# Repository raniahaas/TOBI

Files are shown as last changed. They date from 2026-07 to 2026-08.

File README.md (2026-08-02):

# TOBI
Telemetry, Orientation and Barometric Instrument Flight Computer used for the University of Cincinnati's Rocketry Club's Projects.\
TOBI_Logo

# Introduction
TOBI, from the Japanese word 飛び（とび「tobi」）meaning to soar, was born to serve as a custom avionics bay as a foundation for the University of Cincinnati's Rocketry Club's future space attempt, as well as a custom device personally. The overall goal for final development is to have a working custom flight computer that can log data, determine events, and fire pyrotechniques, all independently.

This repository is still in _**active development**_, but is intended as a clean starting ground to learn, teach, and develop further knowledge of avionics. 

| Goals | Method(s) of Execution |
| --- | --- |
| Multithreading | Using FreeRTOS, use the two cores on the ESP32-S3 to monitor and log events while another core stores data. This became a notable issue in past iterations where often data was missed, overlapped, or entirely logged improperly. |
| Event Logging | More specifically, events for apogee, main and drogue deployment, second-stage ignition, launch, and landing. |
| Pyrotechnics | Simulate the ignition of the second stage, wire cutters, and parachute deployment that current prefab electronics for model rocketry execute. This will become a full feature later on in the following year. |
| Wi-Fi Integration | Mostly, the ESP32 is known for its Wi-Fi capabilities. In our case, I will be utilising the Wi-Fi for data transfer and to check sensor continuity. This will be the main interface that the user uses to communicate with the device externally to the development. |
| Redundancy | Logging the sensors for data and comparing their redundancy with other computers or often COTS components to ensure our code is always performing to the best of its ability while also being the best option financially and methodologically.|

## Project Structure
```
tobiru/
├── data/
│   └── assets/          
│       └── TOBI_Logo.png
├── include/
│   └── flightState.h      # Hardware headers for the flight state
├── lib/                   # Project-specific libraries
├── src/
│   ├── startup/            
|       └── imu_init.cpp   # Initialise IMU datarates
|       └── imu_init.h
|       └── startupSeq.cpp # Start device and initialise accelerometer and barometer datarates; battery voltages
|       └── startupSeq.h
│   ├── globals.h          # Global elements
|   ├── globals.cpp
│   ├── main.cpp           # Task creations
│   └── wifiSetup.h        # Web dashboard with the Wi-Fi interface
├── test/                  # Unity test suites
│   ├── test_flightstate/
|       └── test_main.cpp
│   └── test_telemetry/
|       └── test_main.cpp
└── platformio.ini
```

## Device
| Insturment | Name |
| --- | ---- |
| Accelerometer | [Adafruit LSM6DSO32](https://www.digikey.com/en/products/detail/adafruit-industries-llc/4692/13250946) |
| Microcontroller | [XIAO SEEED ESP32-S3](https://www.digikey.com/en/products/detail/seeed-technology-co-ltd/113991114/19285530) |
| Barometer | [TE MS5611](https://www.digikey.com/en/products/detail/te-connectivity-measurement-specialties/MS561101BA03-50/5277445) |
| PCB | See KiCAD Files |
| Mosfet | [Toshiba T2N7002](https://www.digikey.com/en/products/detail/toshiba-semiconductor-and-storage/T2N7002BK-LM/5409245) |
| Additional elements | Battery terminal, 2-prong screw terminal, 4-prong screw terminal, resistors & transistors | 

## Project Status
- [X] Create multithreaded code for sensor logging (FreeRTOS)
- [X] Have a flight state machine for pre-launch, launch, and landing
- [X] Test functions before final implementation (Unity)
- [X] Local Wi-Fi server for live telemetry data and downloading post-flight data
- [X] PCB integration testing
- [ ] Use pyrotechniques for deploying main and drogue chutes
- [ ] Test flights!

## Building and Flashing Device
The native PlatformIO extension allows the user to flash to the device by simply validating the code and 'pushing' it onto the device. 
Flashing and validating code in Visual Studio Code with PlatformIO
You can additionally flash the code manually by:
```
# Build and upload firmware to the flight computer
pio run -e esp32s3 -t upload

# Open serial monitor
pio device monitor
```

## Flight State
There are three main flight states: startup, ready, and landing. Startup occurs as soon as the device is powered on and will switch to ready once all checks are complete. In the ready state, the user on the front-end server can arm and disarm the device to start recording instruments for flight. Once events are detected and landing has been determined, the device will enter landing mode and produce summary information as well as downloads for CSV files for the user. 

| State | Description |
| ----- | --- |
| startup |	Sensor initialization runs (runStartupSequence()), Wi-Fi starts up |
|ready |	Initialisation complete, device idle, user can access webpage |
| armed	| Event detection is live — launch/apogee/landing checks run every cycle in shutDown()|
| landed	| Landing confirmed; event detection stops, flight summary data is finalised|

Transitions are currently one-directional (no state is re-entered), driven by main.cpp on startup/arm and by the event detection logic on landing confirmation.

## Flight Events
Key flight events are detected by a pure, hardware-independent function (updateFlightState), so the same logic that flies on the device can also be validated on a laptop with no board attached.

| Event | Trigger Condition |
| ----- | --- |
|Launch |	Z-axis acceleration exceeds a threshold (~15 m/s²)|
|Motor Burnout | Gs drop and at least 0.5s have passed |
|Apogee |	Altitude drops more than 50m below the recorded peak|
|Landing | Altitude returns near launch altitude, acceleration stabilises near 1G, device is stable for 3+ seconds|

## Testing
Testing is natively done with the combination of PlatformIO and Unity, where instruments are stripped, and logic functions are tested. Flight-critical logic (launch detection, apogee confirmation, landing verification) is extracted into pure, hardware-independent functions.

```
pio test -e native -f test_flightstate
```
platformio.ini defines two environments inside of testing:
- esp32s3: the physical hardware board the main code runs off of
- native: emulates real hardware to test functions purely

## Safety
This project is intended for use in HPR (high-powered rocketry) and uses pyrotechniques to deploy parachutes and allow for second-stage ignitions. All safety protocols must follow NAR safety codes and are built in accordance with a recoverable HPR two-stage flight. Do not fire, wire, or test pyrotechnic channels without knowledge of the code, device, and user-controlled testing deployment.

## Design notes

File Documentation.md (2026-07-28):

# Beginnings: Multithreading and Sensors
Introductory code and LED development were done by following this article [here](https://randomnerdtutorials.com/esp32-freertos-arduino-tasks/).

Note that the ESP32 being used in the article is slightly different from the one I am using. I am currently running off of the ESP32-S3 by Seeed. 

This is the initial wiring I used following the article. The overarching idea is to specifically assign a core (1 in this case) to blink the LED every second.\ 
Working with one LED on a single core\
The largest trial and tribulation I noted here (other than simply learning how to work with a very basic hardware system) is that the GPIO number for the Seeed is different from the regular Arduino GPIO number. The indexing starts at 1, not 0, which did cause some hairs to be pulled. I then moved to actually working with two cores by using two separate LEDs, one blinking every second on core 1 and another blinking every half second on core 0.
Serial Monitor logging results of multithreading two LEDs.
Additionally, viewed similarly to the stack and heap, not exactly necessary currently, but for more advanced development further down the line, this will become handy.
Serial Monitor outputs of the stack and heap available

# PCB Practice and Development in KiCAD
This section initially follows the tutorials from [HTM Workshop](https://www.youtube.com/playlist?list=PLUOaI24LpvQPls1Ru_qECJrENwzD7XImd) on schematics, custom parts, and PCB design in KiCAD. Initially, this was not a critical piece for the development of TOBI, but overall, for my advancement of knowledge of integration with hardware and understanding the day-to-day activities of an embedded systems engineer, under my mentorship, this was deemed to be a critical step in my knowledge.
### Practising Schematics
The goal here was to re-create a schematic of an SPO2 module in KiCAD. This just helped me get a better lay of the land when it came to working with KiCAD, running the electrical rule checker, ensuring there are no connect flags properly placed, and the general wiring. 
Final SPO2 Module
Additionally, I also learned how to make custom symbols to be added into schematics. Definitely one of the more useful tidbits to know when working with some lesser-known avionics parts. 
Custom MAZ30102 Module for KiCAD
Learned a lot here that consistency is key; often when running checks, I'd run into issues with wiring when setting up the final PCB design. Ensuring everything is consistent saves a lot of hair. Truly covered a lot of bases here: final PCB design (without finishing touches, just drafting), vias, setting up PCB templates based on printing (from the templates [here](https://github.com/sethhillbrand/kicad_templates)), custom schematics for each part as well. 




Screenshot 2026-06-01 at 21 42 16 (2)

## Design and Final Schematics
[TOBI_schematics.pdf](https://github.com/user-attachments/files/28931927/TOBI_schematics.pdf)\
When it actually came to the final schematics for TOBI, it was a smooth process. The majority of the components I was easily able to use and find from previous projects' elements. However, I did run into issues with sourcing the ESP32 from Seeed and the Adafruit DSO32, which both ended up being schematics that I revised from similar components online. \
Edited Adafruit DSO32 Symbol from online sources.\
Another issue I was constantly running into as well with these custom symbols and footprints is that often when I retrieved the KiCAD files from GitHub, if I switched to another branch on the same repository (also known as this one), it would often cause issues with sourcing and retrieving those footprints. 
Custom Footprints in KiCAD, 'Library' displayed on left-hand side, but was often not displayed in the schematics or symbol editor.
One of the first things you should always consider when designing anything in engineering is your constraints, which I did not do this time. Right before reviewing my PCB design, I realised I never considered the fact of my board constraints and where I was placing threaded rod holes for the board. A best solution would be making a 36 mm minimum diameter board, but that is quite the constraint I did not realise would be an issue (in which I am saving for a later date). Out of my two current rockets I would be testing with, the smaller of the two has a 2" diameter for the e-bay.  
Quick PCB layout with the 2in diameter board.
Open rocket design for the smaller kit rocket.
This does pose some great questions on further development, which leaves me with a lot of research and inquiry to do. The first option I can think of is just to make the board double-sided (hence why there are two circles in the image, just for a general feel). Considering how the project has done this previously, I did not consider the fact that the pins from the ESP and the DSO32 would go through the board, meaning this may cause more of an issue stacking the two than I originally thought. I think it is possible to a degree, if I truly do move everything around, but then I'd run into issues with routing, even with vias and such; there would be elements on the bottom that need to be routed up through to the ESP, which may just be exceeding the knowledge I currently have. Another option I considered was giving up and making one solid board to place horizontally instead of vertically inside of the e-bay. The largest issue here now becomes the coding and measurements. It is a lot easier to work off of 0º than +- 90º. When it comes to collecting telemetry data, lock-out angles, & recording information, it becomes an issue. 

### UI Design
Moving on from multithreading, my next focus was then on the front-end since this not only clears up direction for what I need to be monitoring and recording, but also while waiting on the final PCB to be done to test all sensor functions. The majority of my inspiration came from previous use with the Featherweight Altimeter Blueraven App as well as another app called Euristiq. A fun easter egg regarding the colouring is the use of Gunship Grey (676C73), which is the paint colour used on the B-2 Spirit, which is the plane that got be re-introduced into aviation and rocketry. Overall color pallet consists of 6 colors: #C83408, #F5ECD3, #FB961B, #191553, #1E2719, and #676C73. 
Full Figma UI design
I won't go too in-depth into the specifics of the overall UI design; however, I will go through the three main states and their designs. The three states are: Start-up, Ready/Armed, and Landed. First, let's look at our startup. I'm using colours here to help be an indicator of status when it comes to blocks as well as text colours. There is a sort of stoplight system I am using with the Orange, Green, and a lighter shade of the 191553 for a Go, Yield, and Stop system. This is displayed in both the text as well as in the various colored circles littered across each page. Overall system status is displayed in the upper right-hand corner. The full Figma sketch can be viewed [here](https://www.figma.com/board/tCNcCzarbBjb5qSviv4QY5/Untitled--Copy-?node-id=0-1&t=Rhq6jWPLQq2U6YhN-1).
Start up UI design in Figma.\
Similarly, with our Armed and Ready states, we are using colour to display the current status. This status should automatically populate once the start-up sequence is officially complete. The only difference between our Armed and Ready states is the colors--helping to distinguish with the computer determine if it should start looking and watching for a flight to begin. 
Ready and Armed status in Figma.\
Finally, the landing page is where the bulk of the important information is. Often, since we are retrieving this through a WiFi signal and since you stand far from the pad (and through a carbon fiber/fiber glass body tube), it is only when checking the device and arming it that you will see any data. This final screen is the most important since it includes the overall download for the CSV files that will be written from the computer, but also overall quick stats so you can see the key figures from the CSV file. Personally, my favourite as well is an overall curve from launch to landing, which will be a unique challenge to code on the backend.
Landed status in Figma.

# Intermediary: Soldering & Boards
For testing, I ended up soldering pins onto the Adafruit DSO32; this was not only great practice for later when it comes to the actual PCB board, but in general. I had messed up the pins a couple of times since I was originally using unleaded solder instead of leaded and not being overly proficient with soldering caused some issues. Some were not entirely connected, did not contain enough solder, or I had accidentally soldered multiple pins together. Luckily, it was a pretty easy fix and swap to do this properly.\
Unleaded solder of the DSO32\
I had a small setup at my desk that I used to solder, using a space heater with a fan option, my actual soldering iron, and a breadboard to help hold the device in place. Not pictured is my phone as well, on a phone stand, which I used the flashlight for to help focus the light better and give me a cleaner view with the microscope. The flashlight helped tremendously once I had started using it and made the process go by a lot quicker with higher accuracy.\ 

### Final PCB Design
For the most part, the final design went smoothly- the biggest issues arrived after the DRC and when finally sending the Gerber files to JLC PCB. Mainly, the DRC had a lot of issues regarding clearance violations, items shorting, thermal relief connection to zone incomplete, front/back solder mask aperture bridges items with different nets. Clearance and shorting were both easy fixes; they required some more moving around parts and changing the overall nets. However, the thermal relief and solder mask aperture were a little more difficult to understand and fix. They did end up being simple fixes like editing the number of thermal relief holes and adding extra vias to help connect ground points. Additionally, when uploading to JLC, I learned you have to use mounting holes rather than edge cuts, as when uploading the Gerber file, it then sees that as parts rather than a board with cuts.
Front Wiring Design.
Back wiring design.
Front 3D model
Back 3D model
JCL PCB 3D model

## WiFi Integration and testing with breadboard
All of my initial coding was done on [CodePen](https://codepen.io/) to give me faster, live editing of pure HTML without worrying about setting up an environment to run and test this code in. Except for the landing chart, pretty much all is true to the original design that I created in Figma. One notable difference, at least for me, was the fact that I was not able to accurately create the darker grey surrounding boxes for each of the devices being monitored, which is just a result of how I had set up the nesting between each of the elements (has to do with the absolute and relative positioning but then throws off the dynamic part of this). For another iteration of this flight computer's front end, I would love to see if I am able to integrate Svelte at all, since that is mainly where all my front-end development has been in with my courses at the University of Cincinnati. I am using the LittleFS system to mount and write to the CSV (which I will still be doing later in another branch, not the wifi development), and so far have had minimal issues with actually setting that up due to my previous work on a similar setup. 
Serial Monitor displayed information regarding startup and the WiFi server.
Local WiFi Hosting for TOBI, including password protection.
Main startup landing screen, including live data.\
In regard to the live updating, it seems to be working smoothly. You can test the accelerometer by simply moving the board and watching it refresh every second with updated information. Without having the final PCB done, I cannot confirm the battery voltage and/or the barometer data since neither is hooked up currently to the breadboard, but the accelerometer is working smoothly.

# Final Developments
## CAD and E-Bay
All CAD development here is in Fusion360; the goal was to create a rough sketch to have an idea of what the final e-bay should look like and then, from there, create parts individually to print on my A1-Mini.\
Overall e-bay 3D model
Keeping the e-bay vertical was the largest issue that I was concerned with; previously, I had used two 9V batteries housed on a vertical component and on the other side had attached two stratologgers (although that flight had failed, it still worked accordingly with parachute deployment). However, TOBI itself, as a board, sits around the threaded rods and hence needs a housing unit within the electronics bay to attach the LiPo batteries to and hold in place. After some research online, I created this version where there are separate 'boards' creating separation between parts. The LiPo batteries have a compartment they are placed into before placing the top components. There are two options here as well for attaching the batteries to the board: either hard, creating a hole inside of the separation disk in between, or later drilling through the PLA. The PCB will then sit on top of that, keeping it close to the top in case of emergency where the user needs quick access to removal and insertion. The bottom section for now is being left empty, but is a great place for an additional payload and experiment. Spacers are then designed to go around the threaded rods to help house and keep the whole unit in place. Two couplers are on the top and bottom to hold the entire device in place and lock in the threaded rods with the e-bay.  
Closer look at the PCB placement in the e-bay
It ended up taking a couple of modifications to get the couplers correct, with them mainly being undersized based on forgetting the assumption that this does not need a second layer of reinforcement like previous electronics bays I have designed. Since this is pure carbon fibre, it is strong enough to withstand any external acting forces without re-enforcing. After the third version of the coupler, I additionally added threaded rod holes (for a fourth version), LiPo and a separating disk for the inner tube, and more specific measurements for the covers of the internal threaded rods.\
The several 3D printed iterations of couplers.
Final coupler iteration before the threaded rods inside on the electronics bay
Final Iteration for the coupler with the inserted threaded rod holes.
I went through two iterations with the LiPo holders; I noticed that the housing unit was too close to the threaded rod holes and was additionally a little thin on the walls. I slightly adjusted these to be slightly thicker and flipped the unit to sit opposite the threads.
Iterations of LiPo housing unit for electronics bay.
### PCB arrival and Soldering
PCBs came in looking amazing! I had chosen for the overall colour to be red to keep with the theme as a nod to UC and the whole project stemming from UCRC. Although I had already practised soldering earlier with pins on the DSO32, this would be slightly different as I would be using surface mounts (resistors, transistors, and surface-mounted elements like the barometer), which would require hot air soldering instead of regular iron soldering. With new tasks came new materials required to be purchased, so actually soldering the device was delayed by another week more so than I had hoped. 
Back of the final PCB design from JLC PCB
Front of the final PCB design from JLC PCB
One issue I began to notice as I went to place the regular iron devices on the PCB (which later I realised I should not have done first, as the battery terminal and screw switches are likely to melt under the hot air) was that the sizing for the DSO32 was slightly off, making the pin holes millimetres too far to fit snugly. This caused a new cause for concern; this error, I believe, was most likely due to the fact that there is no sizing information listed on Adafruit's website or in the datasheet for the LSMDSO32. Although within the datasheet for the DSO32 are also the LSM6DSOX and ISM330DHCX, which list the sizes for the overall board and the pinouts. Even if I had followed this graph, the pinouts would have been correct, but I measured from edge to edge rather than from pinout to pinout or pinout to edge, leaving a slight give on each side concerning the rest of the board.
Adafruit's Datasheet for the LSMDSO32, LSM6DSOX, and ISM330DHCX
Initially soldered elements on the PCB.
DSO32's width being too small for the large pad size.

### Unit Testing
Although this project has helped me gain knowledge in avionics, embedded systems, PCBs, and an overall understanding of electronics, an additional goal was to further pursue preparation for industry. After researching several positions and keeping track of languages, expected responsibilities, and additional requirements, one recurring responsibility that I realised I had a gap of knowledge in was unit testing. I have previously done unit testing in my co-ops and in other capacities with personal projects; my co-op had used proprietary software, and my own projects were more case tests written natively in the language I was working in. After some research, I came down to two options: Docker and [Unity](https://github.com/ThrowTheSwitch/Unity) (not the engine). After getting sufficiently through using Docker, I realised that Unity was actually native to Platformio and would create easier integration when it came to case testing, and I later switched. However, the biggest issue I will always run into with unit testing is edge cases; these are the most critical since these devices often deal with pyrotechniques, ensuring there isn't a false launch could be detrimental to a flight and cause early parachute deployment (all launches in HPR are manually controlled by a RSO for L1 and L2 launches, more experimental can occur through Tripoli and L3 but for our purposes there can be no false ignition of a motor only early deployment of parachutes and e-matches). To help combat this, I write truth tables in addition to the Unity tests to help demonstrate clearly, based on given information, how the device should perform, then confirm with the Unity code that the device is performing as stated. 
Unit testing truth tables for each function written in Unity.
Final testing for initial unit testing in Unity natively in Platformio.

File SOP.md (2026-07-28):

# Standard Operating Procedure of TOBI
This is a comprehensive checklist for TOBI, a custom avionics flight computer used for HPR (high power rocketry) model rockets. This device is for logging and saving instrument data only, not pyrotechnic parachute deployment. 
## Pre-launch Items:
- Custom Avionics bay
- PCB (ESP, DSO32, barometer)
- LiPo batteries
- USBC cable
- Laptop
- Electronics screwdriver
- Electrical tape

Items to test before launch day:
- Device activates
  - TOBI correctly allows arming device
  - Powers on WiFI & users can connect
  - Live data is running
  - Data rate values are correct
  - TOBI fully runs startup without errors
    - TOBI ensures battery voltage ensure LiPos are charged
- Assembly
  - Ensure no parts on PCB are loose
  - Tighten screw terminals
  - WiFi can be accessed through body tube
- Ensure packing for transit will not cause any items on device to come loose

## Launch Day Procedure:
- Check battery voltages
- Ensure TOBI powers on
  - Ensure live data is running properly
- Lock and load device into ebay
  - Ensure screws are tightened
  - 
### Pad Operations 
**DO NOT ARM DEVICE UNTIL ON PAD**
- Check WiFi Operations
- Once the rocket is on the rails and ready to launch after hooking up the motors, then arm the device for flight

## Recovery
- Ensure all data is downloaded to the user's device before shutting down electronics
- Double-check both CSV files have been downloaded

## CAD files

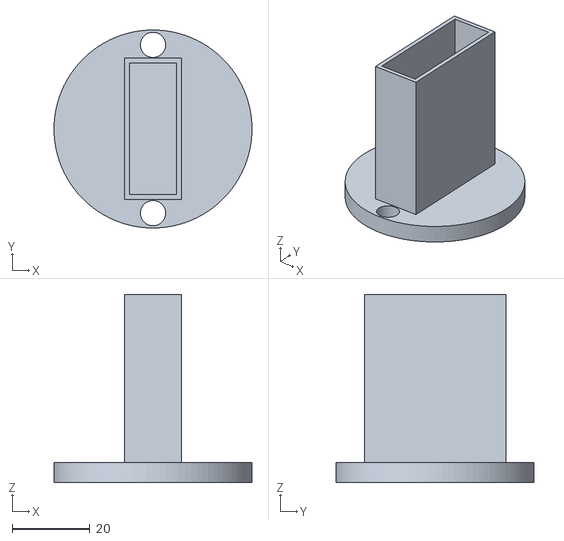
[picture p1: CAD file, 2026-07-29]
CAD_files/testing/LiPo_Holder_TOBI.stl
50.8 x 50.8 x 48.3

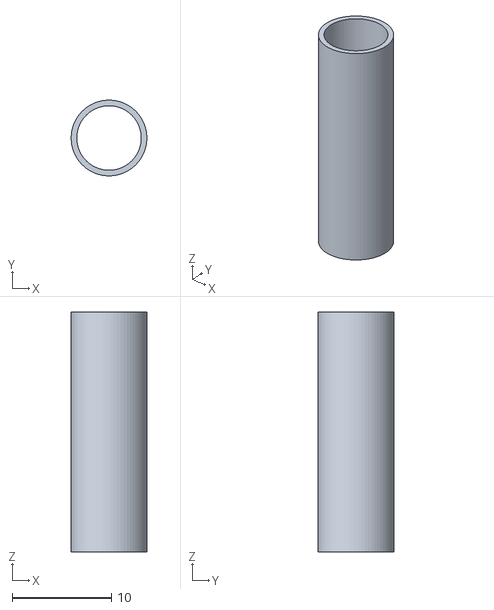
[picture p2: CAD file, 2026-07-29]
CAD_files/Threaded_Rod_Cover.stl
7.62 x 7.62 x 24.1

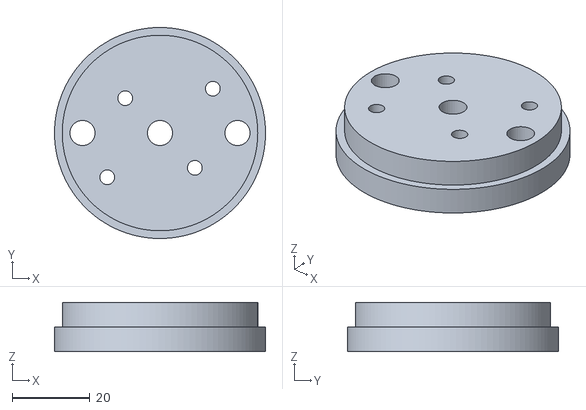
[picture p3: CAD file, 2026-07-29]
CAD_files/TOBI_cupler.stl
54.4 x 54.4 x 12.7

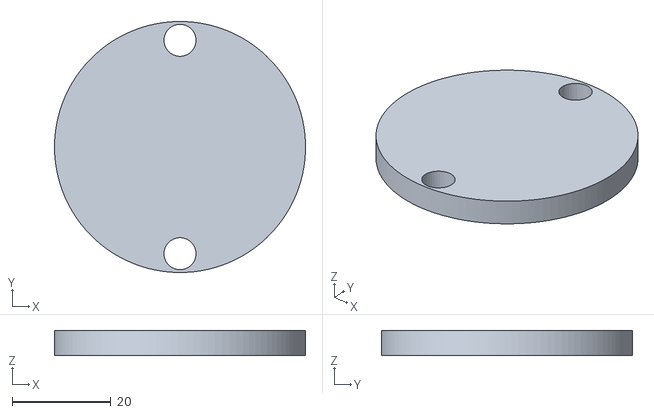
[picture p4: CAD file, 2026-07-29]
CAD_files/Flat_TOBI.stl
50.8 x 50.8 x 5.08

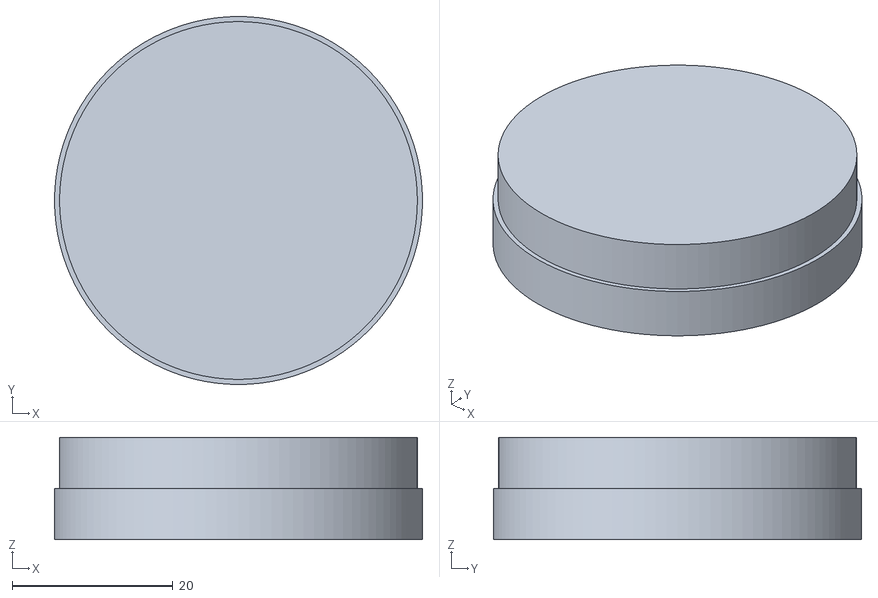
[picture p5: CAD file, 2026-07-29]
CAD_files/testing/TOBI_cupler.stl
45.7 x 45.7 x 12.7

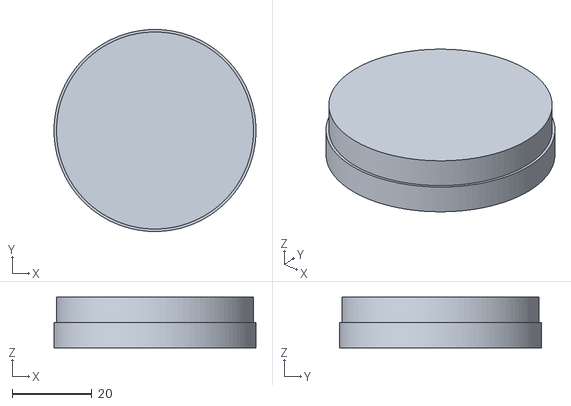
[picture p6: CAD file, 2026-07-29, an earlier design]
CAD_files/testing/TOBI_cupler (1).stl
50.8 x 50.8 x 12.7

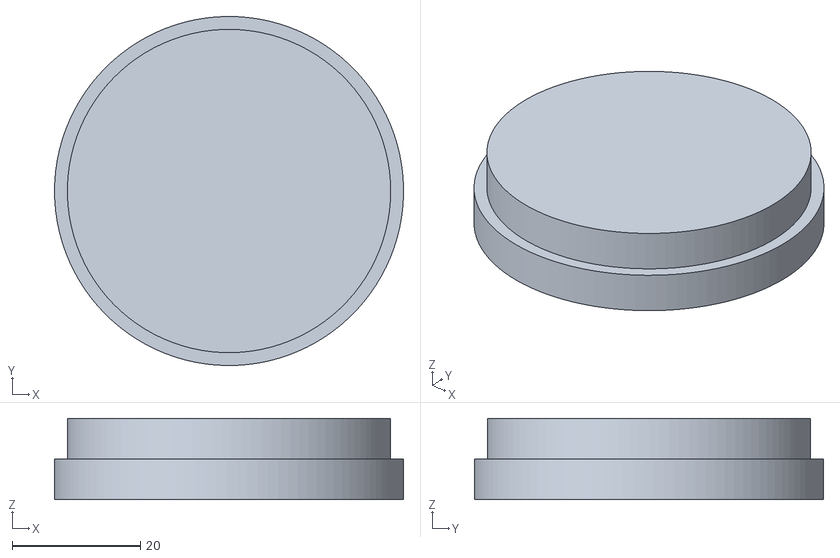
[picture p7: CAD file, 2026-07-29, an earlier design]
CAD_files/testing/TOBI_cupler (2).stl
54.4 x 54.4 x 12.7

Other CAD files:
CAD_files/LiPo_Holder_TOBI.stl

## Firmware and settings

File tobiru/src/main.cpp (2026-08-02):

/**
05/22/2026 - RH - Basework for multithreading integration
06/02/2026 - RH - Fixes to the RTOS declarations
06/14/2026 - RH - Added Startup sequence for IMU
06/14/2026 - RH - Battery Voltage display for serial log
06/16/2026 - RH - Testing for IMU; without battery testing independently
                - Moved Startup function to separate file
06/30/2026 - RH - Wired flightStatus transitions for WiFi dashboard
07/06/2026 - RH - Edits for incoorperating global variables
*/

#include <Arduino.h>
#include <Adafruit_LSM6DSO32.h>
#include <MS5611.h>
#include "startup/startupSeq.h"
#include <SimpleBatteryMonitor.h>
#include "globals.h"
#include "wifiSetup.h"
#include "fileLogging.h"


//Tasks
TaskHandle_t TaskFileLogging;
TaskHandle_t TaskEventLogging;
TaskHandle_t TaskUserTests;
TaskHandle_t TaskShutdown;
TaskHandle_t TaskIMU;
TaskHandle_t TaskBaro;
TaskHandle_t TaskBattery;

const int led1 = 3;
const int led2 = 5;

//Pyro pins for main and drouge; dont forget about offset when testing
const int PYRO_DROUGE = 5;
const int PYRO_MAIN = 9;

//Landed state variables
static float         maxAltitudeSeen    = 0;
static float         launchAltitude     = 0;
static bool          launched           = false;
static bool          apogeeReached      = false;
static unsigned long landedConfirmStart = 0;
static bool burnoutLogged = false;
static bool drogueDeployed = false;
static bool mainDeployed = false;
static unsigned long landingConfirmed = 0;
static unsigned long burnoutTime = 0;

//IMU writing
void imuWrite(void *pvParameters) {
  for (;;) {
    sensors_event_t accel, gyro, temp;
    dso32.getEvent(&accel, &gyro, &temp);

    //Write into globals to modify and grab
    g_accelX = accel.acceleration.x;
    g_accelY = accel.acceleration.y;
    g_accelZ = accel.acceleration.z;

    g_gyroX  = gyro.gyro.x;
    g_gyroY  = gyro.gyro.y;
    g_gyroZ  = gyro.gyro.z;

    logSensors();

    vTaskDelay(pdMS_TO_TICKS(100)); //10Hz
  }
}

//Barometer
void readBarometer(void *pvParameters) {
  for (;;) {
    //Once surface mounts are applied test
    // g_barometer = baro.getPressure();
    vTaskDelay(pdMS_TO_TICKS(100));
  }
}

//Event logging
void writeEvents(void *pvParameters) {
  for (;;) {
    if (flightStatus == "armed") {

    }
  }
}

//File logging
void fileLogging(void *pvParameters) {
  for (;;) {
    // log into csv file
    //csvReady = true; for download
    vTaskDelay(pdMS_TO_TICKS(100));
  }
}

//Landing detection and shutdown
//Landing detection will be separate but required for shutdown as well
void shutDown(void *pvParameters) {
  for (;;) {

    if (flightStatus == "armed") {

      float az  = g_accelZ;
      float alt = g_barometer; //replace with real altitude from baro


      //Detect launch when Z accel spike <1.5G
      if (!launched && az > 15.0f) {
        launched       = true;
        launchAltitude = alt;
        logLaunch();
        Serial.println("LAUNCH DETECTED");
      }

      if (!launched) {
        vTaskDelay(pdMS_TO_TICKS(50));
        continue;
      }

      //Calculate motor burnout based on Gs dropping and at least 0.5s passing
      if (!burnoutLogged && loggingTime() > 500) {
        if(az < 12.0f) {
            burnoutTime = loggingTime();
            burnoutLogged = true;
            logEvents("MOTOR BURNOUT", "Accelerometer", "Acceleration dropping post launch, motor burnout occuring.");
            Serial.println("Motor burnout detected!");
        }
      }

      //Track altitude for apogee
      if (alt > maxAltitudeSeen) {
        maxAltitudeSeen = alt;
      }

      //Detect apogee when device droppes 50m below the peak altitude
      if (launched && !apogeeReached && (maxAltitudeSeen - alt) > 50.0f) {
        apogeeReached = true;
        g_apogee = maxAltitudeSeen;
        logEvents("APOGEE", "Barometer and Accelerometer", "Altitude dropping at least 50 meters below max recorded height.");
        Serial.print("APOGEE DETECTED: ");
        Serial.println(g_apogee);
      }

      //Detect landing when near ground state and stable for 3+s 
      if (apogeeReached && !drogueDeployed) {
        digitalWrite(PYRO_DROUGE, HIGH);
        delay(500);
        digitalWrite(PYRO_DROUGE, LOW);
        drogueDeployed = true;
        g_drogue = alt;
        logEvents("DROGUE_DEPLOYED", "Pyro & Barometer & Accelerometer", "Drogue deployment after e-match.");
        Serial.println("Drogue Deployed!");
      }   

      //Main deployment
      const float MAIN_DEPLOY_ALT = launchAltitude + 150.0f;
      if(drogueDeployed && ! mainDeployed && alt < MAIN_DEPLOY_ALT) {
        digitalWrite(PYRO_MAIN, HIGH);
        delay(500);
        digitalWrite(PYRO_MAIN, LOW);
        mainDeployed = true;
        g_main = alt;
        logEvents("MAIN_DEPLOY", "Pyro & barometer", "Main pyros have been fired");
        Serial.println("MAIN DEPLOYED");
      }
    
      //Landing detection
      if(mainDeployed) {
        bool nearGround = (alt < launchAltitude + 20.0f);
        bool stable     = (abs(az - 9.81f) < 1.0f);

        if (nearGround && stable) {
          if (landedConfirmStart == 0) {
            landedConfirmStart = millis();
          } else if (millis() - landedConfirmStart > 3000) {

            g_timeToApogee = apogeeReached ? (float)loggingTime() : 0;
            g_timeToMain = mainDeployed ? (float)loggingTime() : 0;

            flightStatus = "landed";
            Serial.println("LANDED");
          }
        } else {
          landedConfirmStart = 0;
        }
      }
    }

    //20 Hz for eventes
    vTaskDelay(pdMS_TO_TICKS(50)); 
  }
}


void userTests(void *pvParameters) {
  for (;;) {
    vTaskDelay(pdMS_TO_TICKS(1000));
  }
}

void setup() {
  Serial.begin(115200);
  delay(3000);

  Wire.begin(5, 6);

  //PYRO pins
  pinMode(PYRO_DROUGE, OUTPUT); digitalWrite(PYRO_DROUGE, LOW);
  pinMode(PYRO_MAIN, OUTPUT); digitalWrite(PYRO_MAIN, LOW);

  //Intialise state
  flightStatus = "startup";

  runStartupSequence();
  startWifi();
  loggerInit();

  flightStatus = "ready";

/*
  Core 0:
    Used for all event logging
      File logging
      Events
      User tests
  Core 1:
    All fetching from instruments
      IMU
      Accel/Baro
  */

  //Core 0 Tasks                 
  xTaskCreatePinnedToCore(writeEvents,   "eventLogging", 8192, NULL, 2, &TaskEventLogging, 0);
  xTaskCreatePinnedToCore(fileLogging,   "fileLogging",  4096, NULL, 1, &TaskFileLogging,  0);
  xTaskCreatePinnedToCore(userTests,     "TestMode",     4096, NULL, 1, &TaskUserTests,    0);
  xTaskCreatePinnedToCore(shutDown,      "PoweringOff",  4096, NULL, 1, &TaskShutdown,     0);
 
  //Core 1 Tasks
  xTaskCreatePinnedToCore(imuWrite,      "imu",          4096, NULL, 2, &TaskIMU,          1);
  xTaskCreatePinnedToCore(readBarometer, "barometer",    4096, NULL, 1, &TaskBaro,         1);   

}

void loop() {
  WiFiInterface(); 
}

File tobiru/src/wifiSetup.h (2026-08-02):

/**
06/16/2026 - RH - Moved code to be independent in main
06/30/2026 - RH - Started integration of CodePen HTML setup
06/30/2026 - RH - Fixed JSON shape, string quoting, CSS dedup, function scope
07/06/2026 - RH - Edits for incoorperating global variables as well as more HTML edits
*/
#pragma once
#include <WiFi.h>
#include <WiFiAP.h>
#include <LittleFS.h>
#include "FS.h"
#include "globals.h"
#include "fileLogging.h"

#include <SimpleBatteryMonitor.h>
#include <Adafruit_LSM6DSO32.h>

const char *ssid     = "TOBI";
const char *password = "password";

WiFiServer server(80);

//Full HTML code
const char homePage[] PROGMEM = R"=====(
<!DOCTYPE html>
<html lang="en">
<head>
<meta charset="UTF-8">
<meta name="viewport" content="width=device-width, initial-scale=1.0, viewport-fit=cover">
<link href="https://fonts.googleapis.com/css2?family=Ubuntu+Sans+Mono:ital,wght@0,400..700;1,400..700&display=swap" rel="stylesheet">
<title>TOBI</title>
<style>
  * { margin:0; padding:0; box-sizing:border-box; }

  html, body {
    background:#191553;
    font-family: -apple-system, BlinkMacSystemFont, 'Segoe UI', sans-serif;
    height:100%;
    overflow:hidden;
  }

  #app {
    display:flex;
    flex-direction:column;
    height:100vh;
    height:100dvh;
  }

  .topbar {
    display:flex;
    align-items:center;
    justify-content:space-between;
    padding:12px 16px;
    padding-top:max(12px, env(safe-area-inset-top));
    background:#191553;
    border-bottom:1px solid rgba(255,255,255,0.06);
    flex-shrink:0;
    z-index:10;
  }

  .logo {
    height:28px;
    display:flex;
    align-items:center;
  }

  .logo img {
    height:100%;
    width:auto;
    display:block;
  }

  /* Fallback text if logo hasn't loaded yet */
  .logo-fallback {
    color:#F5ECD3;
    font-size:14px;
    font-weight:700;
    letter-spacing:2px;
  }

  .topbar-right {
    display:flex;
    align-items:center;
    gap:8px;
  }

  .time {
    font-size:11px;
    color:#F5ECD3;
    letter-spacing:0.5px;
    font-variant-numeric: tabular-nums;
  }

  .status-light {
    width:14px;
    height:14px;
    border-radius:50%;
    flex-shrink:0;
  }

  .light-off  { background:#C83408; }
  .light-on   { background:#7FCB8F; }
  .light-busy { background:#FB961B; }

  .pulse-dot { animation: pulse 1.6s ease-in-out infinite; }
  @keyframes pulse { 0%,100%{opacity:1} 50%{opacity:0.4} }

  .scroll-area {
    flex:1;
    overflow-y:auto;
    -webkit-overflow-scrolling:touch;
    scrollbar-width:none;
    padding:14px 14px;
    padding-bottom:max(24px, env(safe-area-inset-bottom));
  }
  .scroll-area::-webkit-scrollbar { display:none; }

  .card {
    background:#676C73;
    border-radius:5px;
    padding:14px 16px;
    margin-bottom:12px;
  }

  .card-label {
    font-size:11px;
    color:#D0F3D3;
    letter-spacing:0.5px;
    margin-bottom:8px;
    text-transform:uppercase;
  }

  .banner {
    background:#F5ECD3;
    border-radius:14px;
    padding:14px 16px;
    margin-bottom:12px;
    display:flex;
    align-items:center;
    justify-content:space-between;
  }

  .banner-text {
    color:#191553;
    font-size:14px;
    font-weight:600;
    line-height:1.3;
  }

  .toggle-btn {
    width:48px;
    height:48px;
    border-radius:50%;
    border:none;
    display:flex;
    align-items:center;
    justify-content:center;
    font-size:10px;
    font-weight:700;
    letter-spacing:0.5px;
    color:#F5ECD3;
    cursor:pointer;
    flex-shrink:0;
  }

  .toggle-off { background:#C83408; }
  .toggle-on  { background:#7FCB8F; color:#191553; }

  .sensor-value {
    font-size:20px;
    font-weight:700;
    color:#312F29;
    text-align:center;
    font-variant-numeric: tabular-nums;
    background:#D0F3D3;
    border-radius:5px;
    border:2px solid #88C493;
    padding:6px 0;
  }

  .triple-row {
    display:grid;
    grid-template-columns: 1fr 1fr 1fr;
    gap:8px;
  }

  .triple-item {
    background:rgba(245,236,211,0.08);
    border-radius:10px;
    padding:10px 6px;
    text-align:center;
  }

  .triple-axis {
    font-size:10px;
    color:#FFFFFF;
    margin-bottom:6px;
    text-transform:uppercase;
    letter-spacing:0.5px;
  }

  .triple-val {
    font-size:15px;
    font-weight:700;
    color:#F5ECD3;
  }

  .triple-unit {
    font-size:9px;
    color:#F5ECD3;
    opacity:0.5;
    margin-top:2px;
  }

  .dl-row {
    display:flex;
    align-items:center;
    gap:10px;
  }

  .dl-btn {
    flex:1;
    background:#F5ECD3;
    color:#191553;
    border:none;
    border-radius:10px;
    padding:12px 0;
    font-size:13px;
    font-weight:600;
    cursor:pointer;
    text-align:center;
    text-decoration:none;
    display:block;
  }

  .dl-status {
    width:48px;
    height:48px;
    border-radius:50%;
    background:#FB961B;
    color:#191553;
    display:flex;
    align-items:center;
    justify-content:center;
    font-size:9px;
    font-weight:700;
    line-height:1.1;
    text-align:center;
    flex-shrink:0;
  }

  .summary-row {
    display:flex;
    justify-content:space-between;
    padding:6px 0;
    border-bottom:1px solid rgba(245,236,211,0.1);
    font-size:12px;
  }
  .summary-row:last-child { border-bottom:none; }
  .summary-key { color:#F5ECD3; opacity:0.65; }
  .summary-val { color:#F5ECD3; font-weight:600; }

  .chart-wrap { margin-bottom:4px; }

  .scroll-hint {
    text-align:center;
    color:#F5ECD3;
    opacity:0.4;
    font-size:14px;
    padding:4px 0;
    animation: bob 1.6s ease-in-out infinite;
    display:none;
  }
  @keyframes bob {
    0%,100% { transform:translateY(0); opacity:0.4; }
    50%      { transform:translateY(4px); opacity:0.8; }
  }

  .conn-status {
    text-align:center;
    font-size:10px;
    color:#F5ECD3;
    opacity:0.3;
    padding:8px 0 4px;
    letter-spacing:0.5px;
  }

</style>
</head>
<body>
<div id="app">
  <div id="topbar-fixed"></div>
  
<div class="scroll-area" id="scroll-area">
    <div id="phone"></div>
    <div class="scroll-hint" id="scroll-hint">&#9660;</div>
    <div class="conn-status" id="conn-status">Connecting to flight computer&hellip;</div>
  </div>
</div>
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

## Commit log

2026-05-22 LED Multithreading
    Simple set-up for setting multithreading up with LEDs
2026-06-03 Function declaration fix
    Properly instantiated the RTOS threading requirements
    [main.cpp]
2026-06-14 IMU Init
    Initial checks for IMU startup dso32, code clear untested with physical device
2026-06-14 Voltage Checks
    Check battery voltage and ensure device is safe to move forward. This is an additional check done by the computer this should be completed by hand with a multimeter before launch. Untested with batte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
2026-06-16 IMU Testing
    Tests for IMU, inside of the setup loop currently all checks are running however when then placed in the core it is dumping. Saving for reference.
2026-06-16 Finished IMU Checks
    IMU checks are currently running, since we are only calling startup once, it was moved to a separate file rather than as a core event; most likely will do a similar idea when it comes to shutdown
2026-06-17 Updated Battery Checks
    Current battery checks are running and working properly when plugged into a computer. This will become more important information and of a check when the webserver is created.
2026-06-17 Final initial threading setup
    Small changes and serial print lines before rebasing and closing ticket
